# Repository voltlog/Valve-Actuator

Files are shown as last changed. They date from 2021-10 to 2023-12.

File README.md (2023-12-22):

# 10ch Valve Actuator (Tasmota compatible)
I designed this 10 channel valve actuator board to be able to control up to 10 electrical valve actuators for my floor heating system. It is based on an ESP32 which makes it Tasmota/MQTT compatible and this allows me to easily integrate it into my HomeaAssistant server. For more information check out [Voltlog #383](https://youtu.be/kZS3ggG0QJI).

If you are looking for sources of previous revisions (revA, revB, revC) checkout the different branches of this repo.

To flash the ESP32 you can use a VoltLink usb/serial converter or you can use your own usb-serial converter module through the on-board JST-SH 1.0mm pitch 6 pin connector. After loading the initial firmware, you can update the firmware via OTA. By default board will ship loaded with Tasmota. 

If you would like to order one of these boards ready assembled, check out my [Tindie store](https://www.tindie.com/products/voltlog/tasmota-esp32-floor-heating-valve-controller/).

## Tasmota template revD (do not use this for previous revisions)
{"NAME":"Voltlog Valve Actuator revD","GPIO":[0,3200,288,3232,0,0,0,0,0,228,229,227,234,0,226,225,0,640,608,224,0,232,231,230,0,0,0,0,233,0,32,0,0,0,0,0],"FLAG":0,"BASE":1}

## WARNING
This board has high-voltage AC present which may cause severe personal injury or death if not handled with care. If you are in doubt, please ask for a profesional to install the system for you.

## Changelog revD
- Added support for powering valves with separate voltage input.
- Switched multiple components to SMD variant for DFM purposes.
- Switched to using JST SH connector for expansion GPIO.

For more defails on revD changes checkout this video [Voltlog #467](https://youtu.be/UIELTaJPIKA).

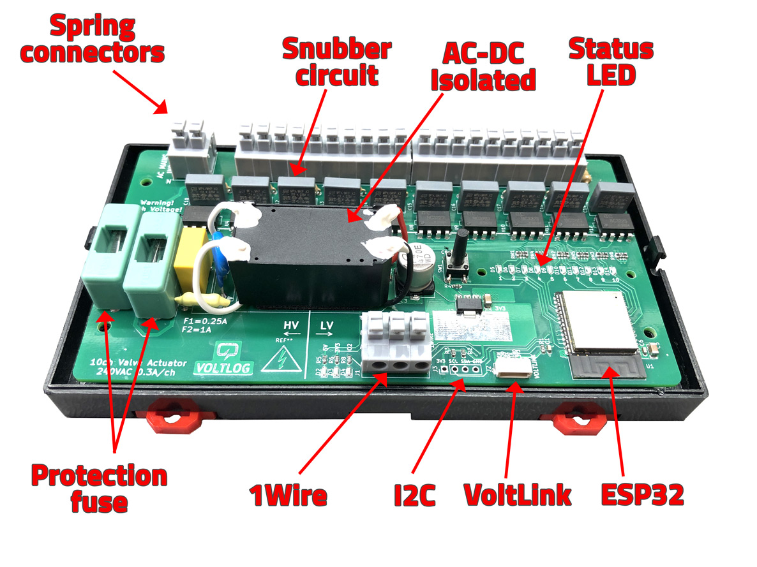
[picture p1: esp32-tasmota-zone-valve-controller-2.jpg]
Image of the assembled PCB


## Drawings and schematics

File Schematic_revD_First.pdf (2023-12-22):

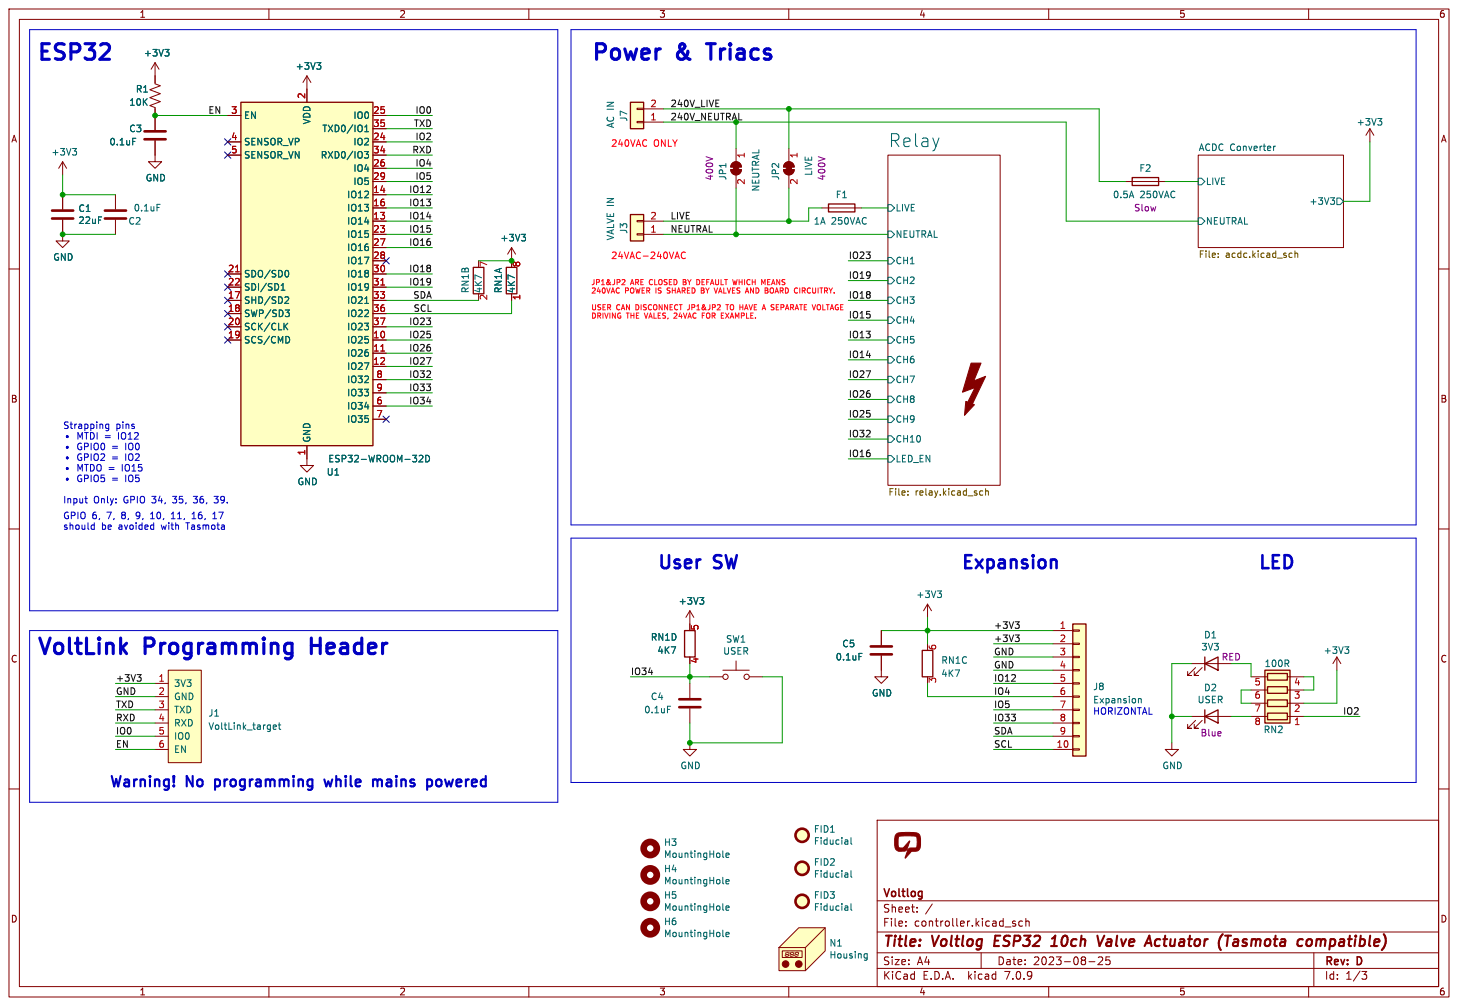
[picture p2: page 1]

2 SCK/CLK 20 SDO/SD0 21 SDI/SD1 22

1 2JP1 NEUTRAL 400V H4 MountingHole H3 MountingHole H5 MountingHole C5

LED_EN
FID3 Fiducial FID1 Fiducial FID2 Fiducial SW1 USER

Id: 1/3 Title: Voltlog ESP32 10ch Valve Actuator (Tasmota compatible) File: controller.kicad_sch Sheet: / Voltlog

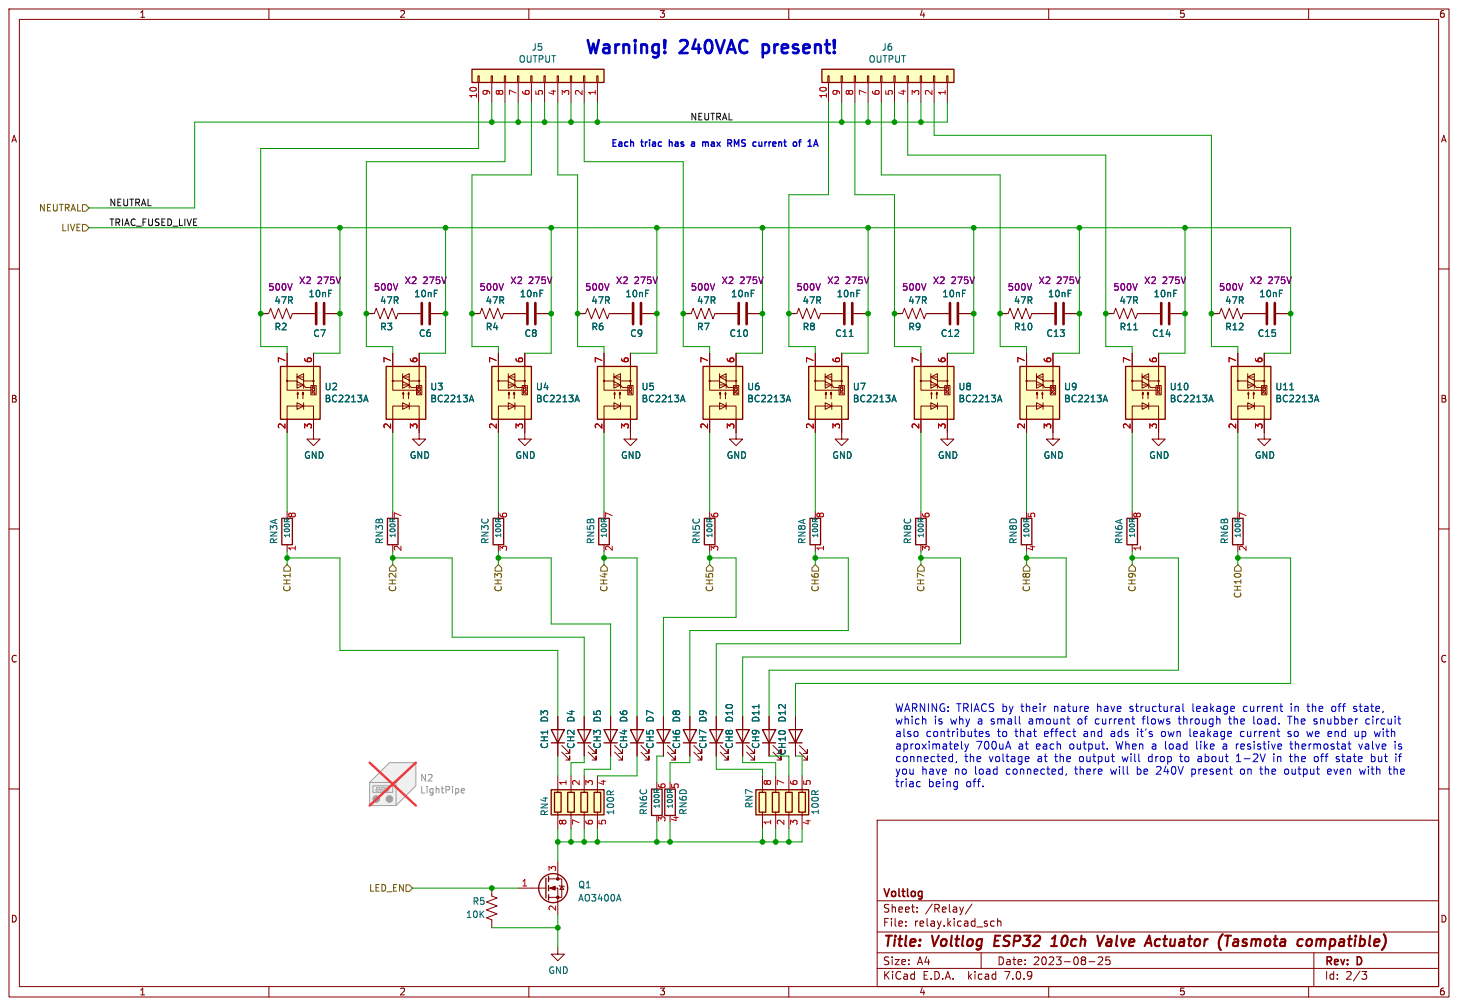
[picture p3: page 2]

Each triac has a max RMS current of 1A

Id: 2/3 Title: Voltlog ESP32 10ch Valve Actuator (Tasmota compatible) File: relay.kicad_sch Sheet: /Relay/

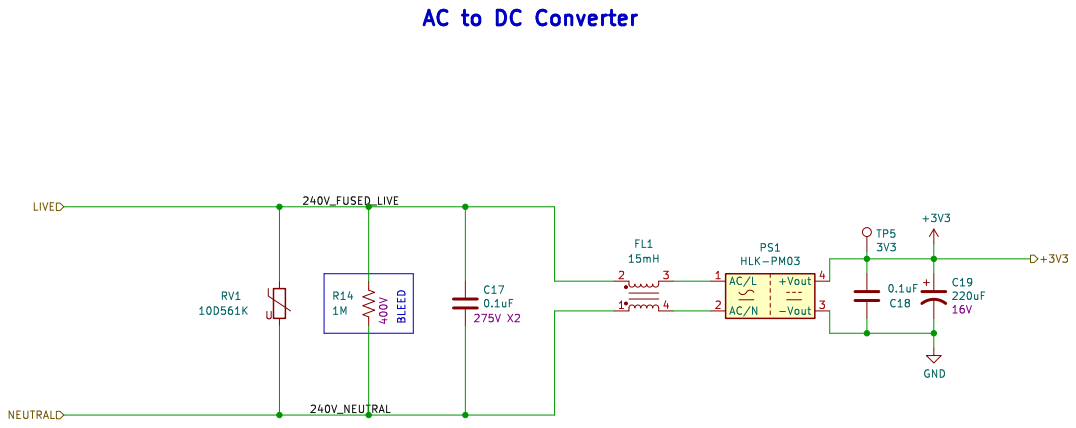
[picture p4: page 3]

Id: 3/3 Title: File: acdc.kicad_sch Sheet: /ACDC Converter/

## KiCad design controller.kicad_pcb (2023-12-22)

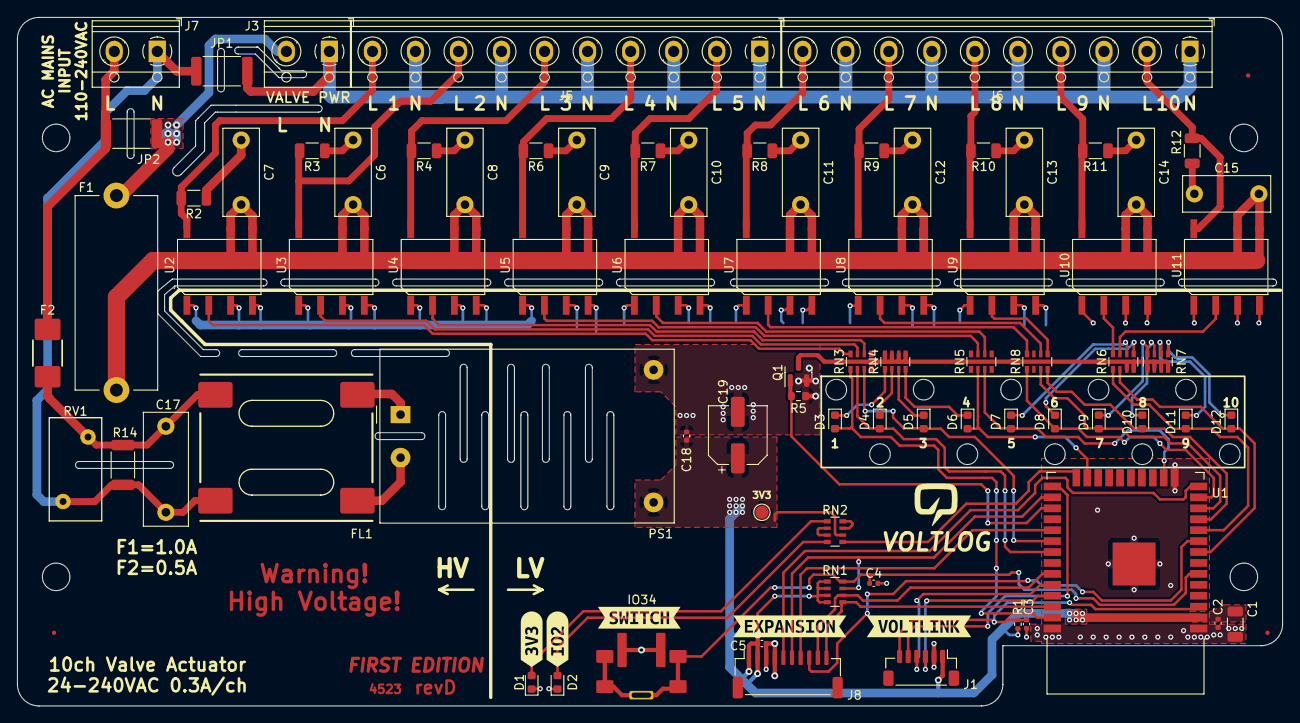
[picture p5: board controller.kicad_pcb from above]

Board: 2 copper layers, 147.0 x 80.0 mm, 93 parts (0 on the bottom side), 78 nets.

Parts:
C1: 22uF; C_1206_3216Metric
C2, C3, C4, C5, C18: 0.1uF; C_0402_1005Metric
C6, C7, C8, C9, C10, C11, C12, C13, C14, C15: 10nF; C_Rect_L10.0mm_W4.0mm_P7.50mm_MKS4
C17: 0.1uF; C_Rect_L13.0mm_W5.0mm_P10.00mm_FKS3_FKP3_MKS4
C19: 220uF; CP_Elec_6.3x7.7
D1: 3V3; LED_0603_1608Metric
D2: USER; LED_0603_1608Metric
D3: CH1; LED_0603_1608Metric
D4: CH2; LED_0603_1608Metric
D5: CH3; LED_0603_1608Metric
D6: CH4; LED_0603_1608Metric
D7: CH5; LED_0603_1608Metric
D8: CH6; LED_0603_1608Metric
D9: CH7; LED_0603_1608Metric
D10: CH8; LED_0603_1608Metric
D11: CH9; LED_0603_1608Metric
D12: CH10; LED_0603_1608Metric
F1: 1A 250VAC; Fuseholder_Cylinder-5x20mm_Stelvio-Kontek_PTF78_Horizontal_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
F2: 0.5A 250VAC; Fuse_2410
FID1, FID2, FID3: Fiducial; Fiducial_0.5mm_Mask1mm
FL1: 15mH; PSSQAQ1212-153M
H3, H4, H5, H6: MountingHole; MountingHole_3.2mm_M3_DIN965
J1: VoltLink_target; VoltLink-vertical
J3: VALVE IN; TerminalBlock_1x02_P5.00mm_Horizontal
J5, J6: OUTPUT; TerminalBlock_1x10_P5.00mm_Horizontal
J7: AC IN; TerminalBlock_1x02_P5.00mm_Horizontal
J8: Expansion; JST_SH_SM10B-SRSS-TB_1x10-1MP_P1.00mm_Horizontal
JP1: NEUTRAL; R_2512_6332Metric
JP2: LIVE; R_2512_6332Metric
N1: Housing; BRT-80005
N2: LightPipe; 1272.1020
PS1: HLK-PM03; Converter_ACDC_HiLink_HLK-PMxx
Q1: AO3400A; SOT-23
R1: 10K; R_0402_1005Metric
R2, R3, R4, R6, R7, R8, R9, R10, R11, R12: 47R; R_1206_3216Metric
R5: 10K; R_0603_1608Metric
R14: 1M; R_2010_5025Metric
RN1: 4K7; R_Array_Convex_4x0603
RN2, RN3, RN4, RN5, RN6, RN7, RN8: 100R; R_Array_Convex_4x0603
RV1: 10D561K; RV_Disc_D12mm_W6.1mm_P7.5mm
SW1: USER; TS1045AD
TP5: 3V3; TestPoint_Pad_D1.5mm
U1: ESP32-WROOM-32D; ESP32-WROOM-32
U2, U3, U4, U5, U6, U7, U8, U9, U10, U11: BC2213A; SOIC-7
V1: VOLTLOG_LOGO; voltlog_silk_5mm
kibuzzard-654A05B0: G***; kibuzzard-654A05B0
kibuzzard-654A05C3: G***; kibuzzard-654A05C3
kibuzzard-654A05E9: G***; kibuzzard-654A05E9
kibuzzard-654A0597: G***; kibuzzard-654A0597
kibuzzard-654A0611: G***; kibuzzard-654A0611

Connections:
+3V3: C1.1, C2.2, C5.1, C18.2, C19.1, J1.1 (3V3), J8.1, J8.2, PS1.4 (+Vout), R1.2, RN1.5 (R4.2), RN1.6 (R3.2), RN1.7 (R2.2), RN1.8 (R1.2), RN2.2 (R2.1), TP5.1, U1.2 (VDD)
/240V_LIVE: F2.2, J7.2, JP2.1 (A)
/240V_NEUTRAL: C17.2, FL1.1, J7.1, JP1.1 (A), R14.2, RV1.2
/ACDC Converter/240V_FUSED_LIVE: C17.1, F2.1, FL1.2, R14.1, RV1.1
/EN: C3.1, J1.6 (EN), R1.1, U1.3 (EN)
/IO0: J1.5 (IO0), U1.25 (IO0)
/IO2: RN2.1 (R1.1), U1.24 (IO2)
/IO4: J8.6, RN1.3 (R3.1), U1.26 (IO4)
/IO5: J8.7, U1.29 (IO5)
/IO12: J8.5, U1.14 (IO12)
/IO13: D7.2 (A), RN5.3 (R3.1), U1.16 (IO13)
/IO14: D8.2 (A), RN8.1 (R1.1), U1.13 (IO14)
/IO15: D6.2 (A), RN5.2 (R2.1), U1.23 (IO15)
/IO16: Q1.1 (G), R5.2, U1.27 (IO16)
/IO18: D5.2 (A), RN3.3 (R3.1), U1.30 (IO18)
/IO19: D4.2 (A), RN3.2 (R2.1), U1.31 (IO19)
/IO23: D3.2 (A), RN3.1 (R1.1), U1.37 (IO23)
/IO25: D11.2 (A), RN6.1 (R1.1), U1.10 (IO25)
/IO26: D10.2 (A), RN8.4 (R4.1), U1.11 (IO26)
/IO27: D9.2 (A), RN8.3 (R3.1), U1.12 (IO27)
/IO32: D12.2 (A), RN6.2 (R2.1), U1.8 (IO32)
/IO33: J8.8, U1.9 (IO33)
/IO34: C4.1, RN1.4 (R4.1), SW1.1, U1.6 (IO34)
/LIVE: F1.1, J3.2, JP2.2 (B)
/NEUTRAL: J3.1, J5.1, J5.3, J5.5, J5.7, J5.9, J6.1, J6.3, J6.5, J6.7, J6.9, JP1.2 (B)
/RXD: J1.4 (RXD), U1.34 (RXD0/IO3)
/Relay/TRIAC_FUSED_LIVE: C6.2, C7.2, C8.2, C9.2, C10.2, C11.2, C12.2, C13.2, C14.2, C15.2, F1.2, U2.5, U2.6, U3.5, U3.6, U4.5, U4.6, U5.5, U5.6, U6.5, U6.6, U7.5, U7.6, U8.5, U8.6, U9.5, U9.6, U10.5, U10.6, U11.5, U11.6
/SCL: J8.10, RN1.1 (R1.1), U1.36 (IO22)
/SDA: J8.9, RN1.2 (R2.1), U1.33 (IO21)
/TXD: J1.3 (TXD), U1.35 (TXD0/IO1)
GND: C1.2, C2.1, C3.2, C4.2, C5.2, C18.1, C19.2, D1.1 (K), D2.1 (K), J1.2 (GND), J8.3, J8.4, PS1.3 (-Vout), Q1.2 (S), R5.1, SW1.2, U1.1 (GND), U1.15 (GND), U1.38 (GND), U1.39 (GND), U2.1, U2.3, U2.4, U3.1, U3.3, U3.4, U4.1, U4.3, U4.4, U5.1, U5.3, U5.4, U6.1, U6.3, U6.4, U7.1, U7.3, U7.4, U8.1, U8.3, U8.4, U9.1, U9.3, U9.4, U10.1, U10.3, U10.4, U11.1, U11.3, U11.4
unnamed: C6.1, R3.1
unnamed: C7.1, R2.1
unnamed: C8.1, R4.1
unnamed: C9.1, R6.1
unnamed: C10.1, R7.1
unnamed: C11.1, R8.1
unnamed: C12.1, R9.1
unnamed: C13.1, R10.1
unnamed: C14.1, R11.1
unnamed: C15.1, R12.1
unnamed: D1.2 (A), RN2.5 (R4.2)
unnamed: D2.2 (A), RN2.8 (R1.2)
unnamed: D3.1 (K), RN4.1 (R1.1)
unnamed: D4.1 (K), RN4.2 (R2.1)
unnamed: D5.1 (K), RN4.3 (R3.1)
unnamed: D6.1 (K), RN4.4 (R4.1)
unnamed: D7.1 (K), RN6.6 (R3.2)
unnamed: D8.1 (K), RN6.5 (R4.2)
unnamed: D9.1 (K), RN7.8 (R1.2)
unnamed: D10.1 (K), RN7.7 (R2.2)
unnamed: D11.1 (K), RN7.6 (R3.2)
unnamed: D12.1 (K), RN7.5 (R4.2)
unnamed: J5.2, R7.2, U6.7
unnamed: J5.4, R6.2, U5.7
unnamed: J5.6, R4.2, U4.7
unnamed: J5.8, R3.2, U3.7
unnamed: J5.10, R2.2, U2.7
unnamed: J6.2, R12.2, U11.7
unnamed: J6.4, R11.2, U10.7
unnamed: J6.6, R10.2, U9.7
unnamed: J6.8, R9.2, U8.7
unnamed: J6.10, R8.2, U7.7
unnamed: FL1.3, PS1.1 (AC/L)
unnamed: FL1.4, PS1.2 (AC/N)
unnamed: Q1.3 (D), RN4.5 (R4.2), RN4.6 (R3.2), RN4.7 (R2.2), RN4.8 (R1.2), RN6.3 (R3.1), RN6.4 (R4.1), RN7.1 (R1.1), RN7.2 (R2.1), RN7.3 (R3.1), RN7.4 (R4.1)
unnamed: RN2.6 (R3.2), RN2.7 (R2.2)
unnamed: RN2.3 (R3.1), RN2.4 (R4.1)
unnamed: RN3.8 (R1.2), U2.2
unnamed: RN3.7 (R2.2), U3.2
unnamed: RN3.6 (R3.2), U4.2
unnamed: RN5.7 (R2.2), U5.2
unnamed: RN5.6 (R3.2), U6.2
unnamed: RN6.8 (R1.2), U10.2
unnamed: RN6.7 (R2.2), U11.2
unnamed: RN8.8 (R1.2), U7.2
unnamed: RN8.6 (R3.2), U8.2
unnamed: RN8.5 (R4.2), U9.2

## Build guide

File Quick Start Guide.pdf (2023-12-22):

rev.B Feb-2023

## ESP32 Tasmota/ESPHome Compatible Valve Controller

### Quick Start Guide

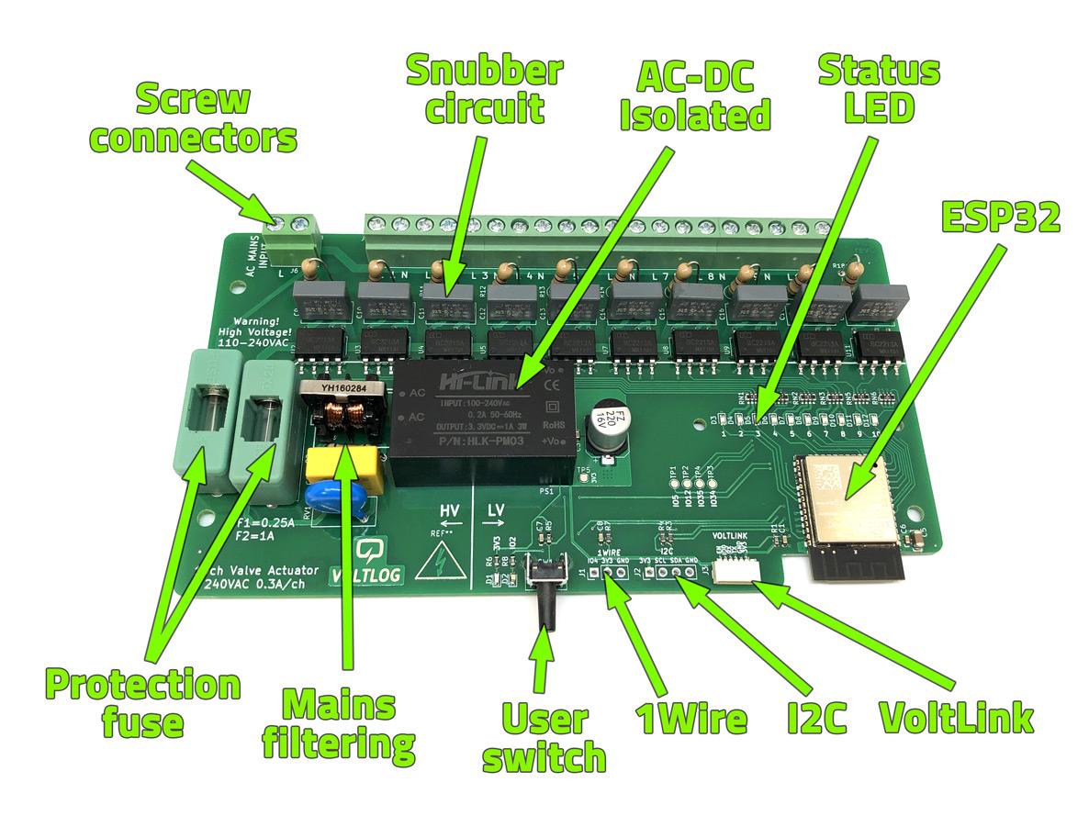
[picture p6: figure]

## Electrical Specs

- Input voltage: 110V-240V AC.
- Output current: up to 0.9A RMS per triac output and up to 2A total combined.
- Low voltage side overcurrent protection: 0.25A slow blow.
- Operating temperature range (ambient): 0-70°C relative humidity 10-80%.
- Screw connector applicable wire: 24-14AWG.
- Internal or optional external higher gain antenna.

## Firmware

Board comes pre-flashed with Tasmota, just apply power and connect to the wireless access point named tasmota_XXXXXX then in your browser go to http://192.168.4.1 to access the Tasmota WebUI.

## Wiring diagram

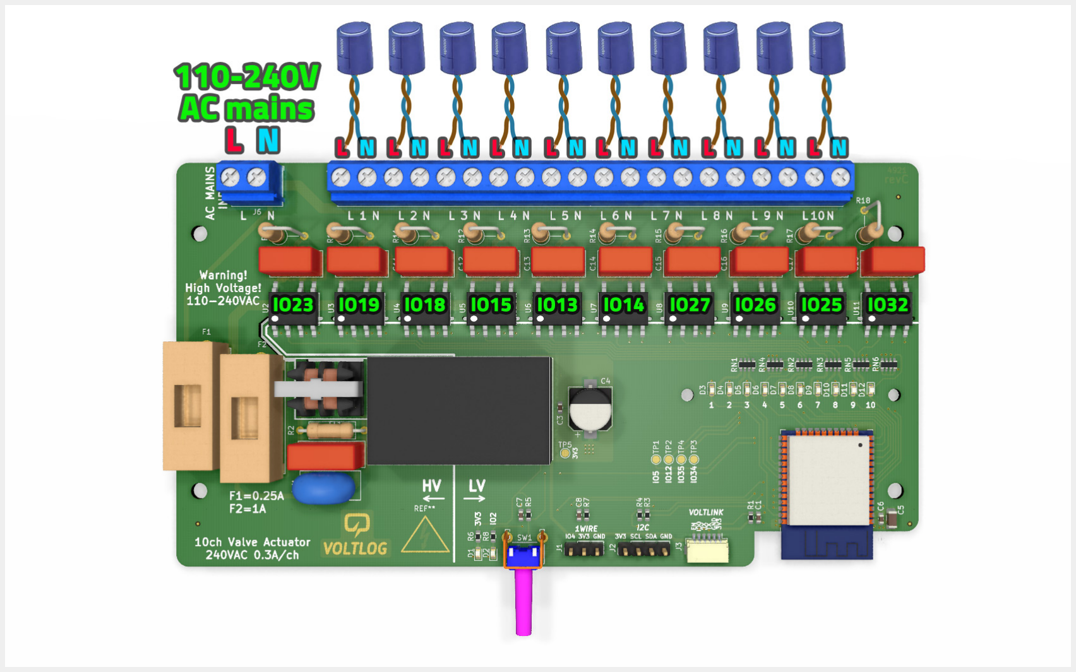
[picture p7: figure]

## Expansion Ports

The board features a few expansion ports for UART, I2C, 1Wire and some GPIO exposed via small test pads. These can be used to connect external sensors and devices to expand the functionality of the controller board.

UART

UART expansion can be accomplished through the use of the VoltLink connector which features the following pinout: EN, IO0, RXD/IO3, TXD/IO1, GND, 3V3. The current sourcing capability on the 3V3 pin of this port is 100mA max.

I2C

I2C expansion port features 4 pins: 3V3, SCL/IO22, SDA/IO21, GND. The current sourcing capability on the 3V3 pin of this port is 100mA max.

1WIRE

1WIRE expansion port features 3 pins: DATA/IO4, 3V3, GND. DATA pin features a discrete 4K7 pull-up resistor. The current sourcing capability on the 3V3 pin of this port is 100mA max.

GPIO

General purpose IO expansion can be accomplished via the small round test pads which connect to the following GPIO: IO5, IO12, IO35, IO34.

## Safety Warnings

This controller board is a DIY type of system and not a ready to go solution. There is an effort required on your side to configure this and get it working in your particular setup. Because this is a DIY project with no safety ratings or approvals, it’s best if you don’t leave it running unattended as I am not responsible for any consequences it might cause.

This controller board uses mains voltage so you need to know what you are doing, otherwise, there is a high risk of electrical shock and/or fire. This is a serious topic, if you are not sure what you are doing, ask for help from an electrician. Every connection should be double checked before applying mains power.

Operation of this equipment in a residential environment could cause radio interference.

If you plan to use the board on a different mains voltage, like 110V or with a different valve actuator with different specs, fuses will need to be adjusted accordingly and F2 can be increased up to 2A which is the limit of the PCB traces.

The 3V3 power brick which powers the control board is isolated and the triacs also provide optical isolation between the ESP32 and the mains side however if you want to be absolutely sure there is no risk of electrical shock I would recommend keeping the board disconnected from mains power during wired programming and supplying external 3V3 power via the Voltlink connector.

## Wifi antenna warning

If you ordered the external antenna option, do not power on the board before connecting the external antenna as doing so could damage the RF section of the ESP32.

More info like schematics, board files, Tasmota template can be found on Github: https://github.com/voltlog/Valve-Actuator

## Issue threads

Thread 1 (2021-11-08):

AC-IN clamp labled wrong

frfrh, 2021-11-08:
It looks like the Labels on the AC-IN clamp are reversed, so the one which should be labled `N` actually has the lable `L` which mean even when blowing the fuses all the board will still have full live on everything which is supposed to be neutral which can be a huge safety issue.

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

voltlog, 2021-11-09:
Thanks for reporting this issue. There is now a mention of this in the README and I will address the issue in the next revision.

Closed 2021-11-09.

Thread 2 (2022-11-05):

Naming switches

phaethon, 2022-11-05:
Under Tasmota "Configure Other" I can give names to switches, but only for switches 1 to 8. Is it issue with Tasmota or with the template I took from Readme in this repository?

phaethon, 2022-11-05:
Probably answered by https://github.com/arendst/Tasmota/discussions/16768

voltlog, 2023-05-11:
This is a limitation of Tasmota, not of this project.

Closed 2023-05-11.

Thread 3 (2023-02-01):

GPIO pins

ClausMunch, 2023-02-01:
Could you describe what GPIO to use for the GPIO pins on the board?
I think I have traced it back to GPIO 21 (SDA) and GPIO 22 (SCL), but I'm not having much luck turning on a small OLED on this (also tested it with a generic ESP32, where it works)

ClausMunch, 2023-02-01:
What I acutally wanted to do, was to have a small OLED through the housing, able to cycle through some basic info (IP, valve status, temperature), with the ability to toggle the display on and off with the onboard button.
Maybe add a temperature sensor on the one wire, to be able to monitor the temperature in the utility space.

Hope it makes sense :)

voltlog, 2023-02-02:
I2C pins are IO21/SDA and IO22/SCL with more information regarding GPIO available in the PDF schematic included in this repo: https://github.com/voltlog/Valve-Actuator/blob/main/Schematic_revC.pdf

I am also going to update the quick start guide to include information about this as I guess most people look there first.

I am going to close this issue now.

Closed 2023-02-02.

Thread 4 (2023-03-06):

[QUESTION] Is possible connected with HVAC?

limkinZero, 2023-03-06:
Hi,

I'm looking for something to allow me control my valvules of floor heating.  Currently, I've a board (Möhlenhoff Alpha-Basis) where the actuators and thermostats are connected. Also, there is an output to connect with my HVAC machine for it to activate the water pump. Is it possible somehow to connect it to the voltlog board?

voltlog, 2023-03-06:
Hi,
This is not an issue with the current published design.

Please note that this design is for advanced users and whether or not extra functionality can be obtained by interconnecting with other systems is something you will have to figure out on your own.

brainstormi, 2024-12-25:
Hi @voltlog...
   Could you confirm how to send the signal to the pump to power on taking into account this works as a dry contact... ? Taking a look at the board I'm not sure how this would be done

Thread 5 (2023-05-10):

Adding switch to boiler

charlesdmir, 2023-05-10:
First, this project is great!
What I'm seeing missing is the switch to control the boiler, meaning when at least one valve is open, it should turn on the switch for the boiler to start.

voltlog, 2023-05-11:
This is not an issue with current design.

Closed 2023-05-11.

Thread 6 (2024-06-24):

Problems with version 2024.6.1 Jun 21 2024

rodrigonogueras, 2024-06-24:
Hello,

I use your Valve-Actuator for more than a year. I usually upgrade the firmware when ESPHome release a new version. I did not have any problem during all this time.

Since I upgraded to 2024.6.1 Jun 21 2024 it ask me to make some changes. For example
1. on OTA I have to put platform

ota:
  - platform: esphome
    password: "xxxxxxxxxxxxxxx"

2. I have to chage dallas to on_wire

Previous
dallas:
  - pin: GPIO4
    update_interval: 5s

Now:
one_wire:
  - platform: gpio
    pin: GPIO4
#    update_interval: 5s

4. On sensor I have to change dallas to dallas_temp
Previous
sensor:
  - platform: dallas_temp
    address: 0xe60922549523b021
    name: P-1 Temp impulsion

Now:
sensor:
  - platform: dallas_temp
    address: 0xe60922549523b021
    name: P-1 Temp impulsion
    update_interval: 5s

Since this change I see lots of Reset Reason = Timer Group 1 Watch Dog Reset Digital Core and the valves are not working well because it loose the connectivity.

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

I don't know if you can help with this problem.

This is the code of one of them:
###########################
esphome:
  name: voltlog-p-1
  friendly_name: voltlog-p-1

esp32:
  board: esp32dev
  framework:
    type: arduino

# Enable logging
logger:

# Enable Home Assistant API
api:
  encryption:
    key: "xxxxxxxxxxxxxxxx"

ota:
  - platform: esphome
    password: "xxxxxxxxxxxxxxxx"

wifi:
  ssid: !secret wifi_ssid
  password: !secret wifi_password

  # Enable fallback hotspot (captive portal) in case wifi connection fails
  ap:
    ssid: "Voltlog-P-1 Fallback Hotspot"
    password: "xxxxxxxxxxxxxxxx"

  # Optional manual IP
  manual_ip:
    static_ip: 192.168.1.142
    gateway: 192.168.1.1
    subnet: 255.255.255.0
    dns1: 1.1.1.1
    dns2: 8.8.8.8

captive_portal:

#MQTT
mqtt:
  broker: !secret mqtt_host
  port: 1883
  topic_prefix: sensores/voltlog/voltlog-p-1
  username: !secret mqtt_username
  password: !secret mqtt_password
  log_topic:
    topic: debug
    level: none

switch:
  - platform: gpio
    pin: 23
    name: Valvula 01
  - platform: gpio
    pin: 19
    name: Valvula 02
  - platform: gpio
    pin: 18
    name: Valvula 03
  - platform: gpio
    pin: 15
    name: Valvula 04
  - platform: gpio
    pin: 13
    name: Valvula 05
  - platform: gpio
    pin: 14
    name: Valvula 06
  - platform: gpio
    pin: 27
    name: Valvula 07
  - platform: gpio
    pin: 26
    name: Valvula 08
  - platform: gpio
    pin: 25
    name: Valvula 09
  - platform: gpio
    pin: 32
    name: Valvula 10

one_wire:
  - platform: gpio
    pin: GPIO4
#    update_interval: 5s

sensor:
  - platform: dallas_temp
    address: 0xe60922549523b021
    name: P-1 Temp impulsion
    update_interval: 5s

  - platform: dallas_temp
    address: 0xe80822546f73c121
    name: P-1 Temp retorno
    update_interval: 5s

# substitutions
substitutions:
  devicename: "voltlog-p-1"
  friendlyname: "voltlog-p-1"

packages:
  text-sensor: !include diag/diag-text-sensor.yaml
  switch: !include diag/diag-switch.yaml
  sensor: !include diag/diag-sensor.yaml

debug:
  update_interval: 5s

###########################

Thanks for your help.

voltlog, 2024-06-24:
Unfortunately I can't help with this because according to your findings it is not a hw problem but something to do with the firmware. I would say revert back to a previous known working version of firmware and don't upgrade.

You could also try to get help by going to ESPHome Discord/Github and post the issue there.

Personally I never upgrade my devices for no good reason, if it works, it doesn't need an update.

rodrigonogueras, 2024-06-24:
OK, Thanks.

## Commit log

2021-11-09 Updated Readme
    Updated readme to mention silkscreen issue on J6.
2021-12-12 RevC initial release
    [BOM.csv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]
2022-04-04 Added schematic in PDF format
2023-12-22 Release revE First Edition
    [acdc.kicad_sch, controller.kicad_pcb, controller.kicad_sch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]
2023-12-22 cleanup revD-first
    [BOM.csv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]
2024-01-24 added missing block
    [relay.kicad_sch]
